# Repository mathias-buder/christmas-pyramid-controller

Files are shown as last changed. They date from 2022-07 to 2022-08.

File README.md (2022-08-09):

- [Introduction](#introduction)
- [The Christmas Pyramid](#the-christmas-pyramid)
- [Control Unit Design](#control-unit-design)
  - [Requirement Definition](#requirement-definition)
  - [System Architecture](#system-architecture)
    - [CPU Board](#cpu-board)
  - [Sound Card](#sound-card)
  - [UART-RF Bridge](#uart-rf-bridge)
  - [Electronical Design](#electronical-design)
  - [Final Device Layout](#final-device-layout)
  - [Software Architecture](#software-architecture)
    - [Software Layer Stackup](#software-layer-stackup)
    - [Source Code Layout](#source-code-layout)
    - [Persistent Memory Scheme](#persistent-memory-scheme)
    - [Main Control Loop Flow](#main-control-loop-flow)
  - [Command Line Interface](#command-line-interface)
    - [Command Structure](#command-structure)
    - [Output Format](#output-format)
      - [Real-Time Clock / Temperature](#real-time-clock--temperature)
      - [Task List](#task-list)
    - [Command List](#command-list)

# Introduction
Some time ago, my dad called me to tell me that he is planing to build a giant christmas pyramid that is supposed to be placed in front of the local church at christmas time. The setting up should take place in the form of a Christmas party where everyone comes together and drinks mulled wine.

**What a great idea I thought!**

As the pyramid was to remain standing for the entire Christmas season, a control unit was needed for automatic operation.

# The Christmas Pyramid
As can be seen below, the pyramid contains a number of lamps (230 VAC) as well as a motor (230 VAC) for turning the wings.

<p align="center">

</p>

# Control Unit Design
This section is going to describe the control unit design process.

## Requirement Definition
The ECU shall satisfy the following list of requirements:
- Shall have the ability to switch multiple 230 VAC actors (at least 2 individually)
- Shall have to ability to detect motion from humans that move in front of the pyramid
- Shall be able to play music
  - that is stored on an SD Card / USB thumb drive
  - that is in .mp3 and .wav format
  - that is automatically played based on motion sensor input
  - that is outputted through a standard 3.5mm audio jack to be fed to an audio amplifier
- shall have an interface to re-programmed the firmware image
- shall have the ability to be accessed over the air
- shall have the ability to setup tasks in which the user can specify
  - task activation/deactivation time
  - is music playback active/inactive
  - duration of music playback
  - is motion detection active/inactive
  - which AC-actor switch shall be active/inactive
- Shall operate within the temperature range of -20°C - 40°C

## System Architecture
The overall system architecture is shown in the block diagram below. The basic idea is to use as many off-the-shelf components as possible and interconnect them using a custom designed carrier board.

1. 80 MHz ARM Cortex-M4 µC TM4C123GH6PMI
2. Two-line dot-matrix display NHD-0216K3Z-NSW-BBW-V3
3. Endless rotary push encoder
4. UART-RF radio module HM-TRP
5. SD card interface 
6. USB 2.0 interface 
7. Sound card with VSI 003 audio codec
8. Real-time clock (incl. temperature sensor) DS3231
9. EEPROM 32KByte
10. 8-channel relay board (230VAC IOA)
11. Infrared motion sensor HCSR501

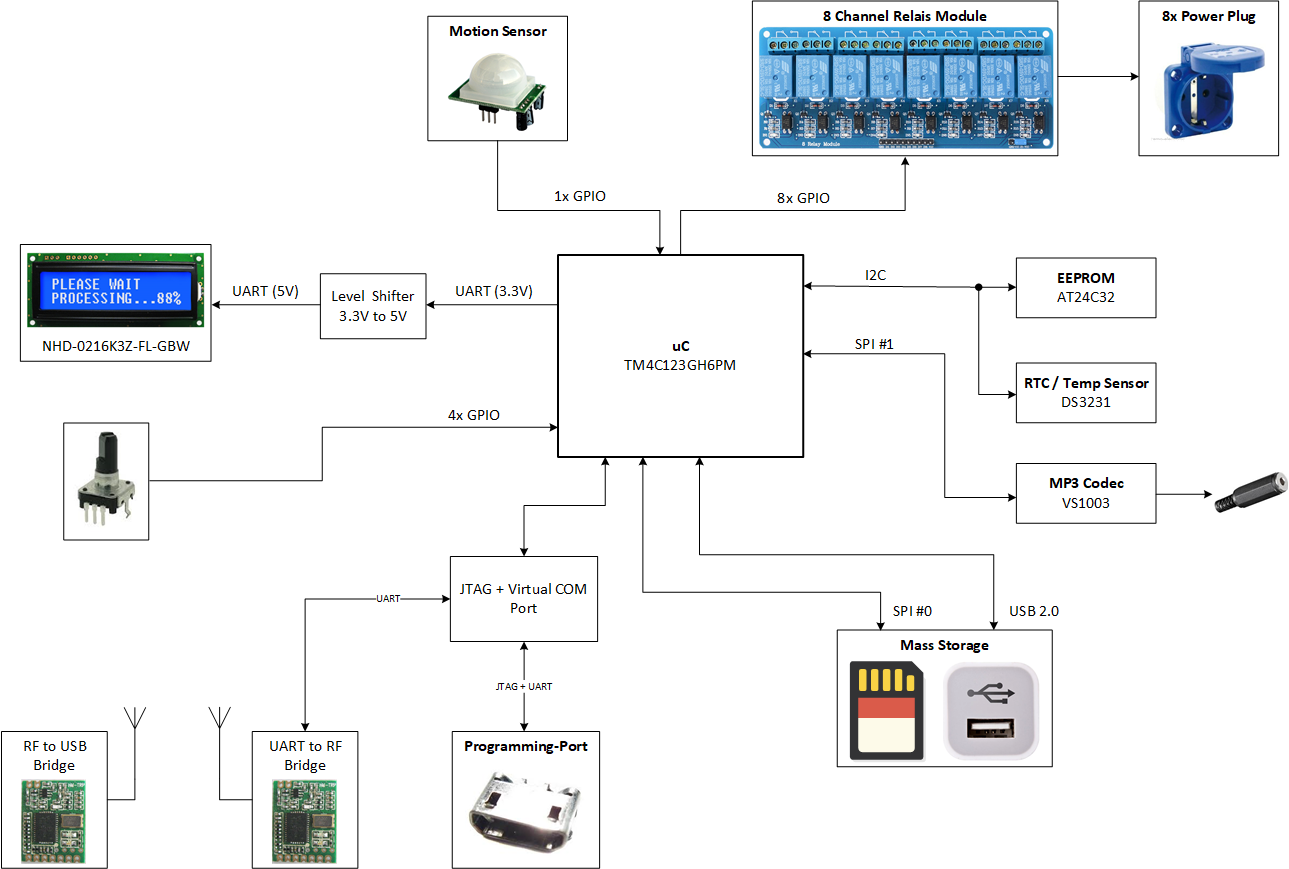
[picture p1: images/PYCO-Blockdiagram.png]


### CPU Board
As central processing unit the evaluation kit [EK-TM4C123GXL](https://www.ti.com/tool/EK-TM4C123GXL) from TI has been used. This board offers:

* 80 MHz ARM Cortex-M4 (TM4C123GH6PMI)
* On-Board ICD (JTAG) incl. an virtual serial port over a single USB connection
* USB 2.0 interface for e.g. mass-storage interface
* On-Board clocking incl. LFO for real-time clock applications
* Rich expansion header to interface with all available peripherals
* Rich, free and easy-to-use API provided by TI
* __Cost on 10 EUR__

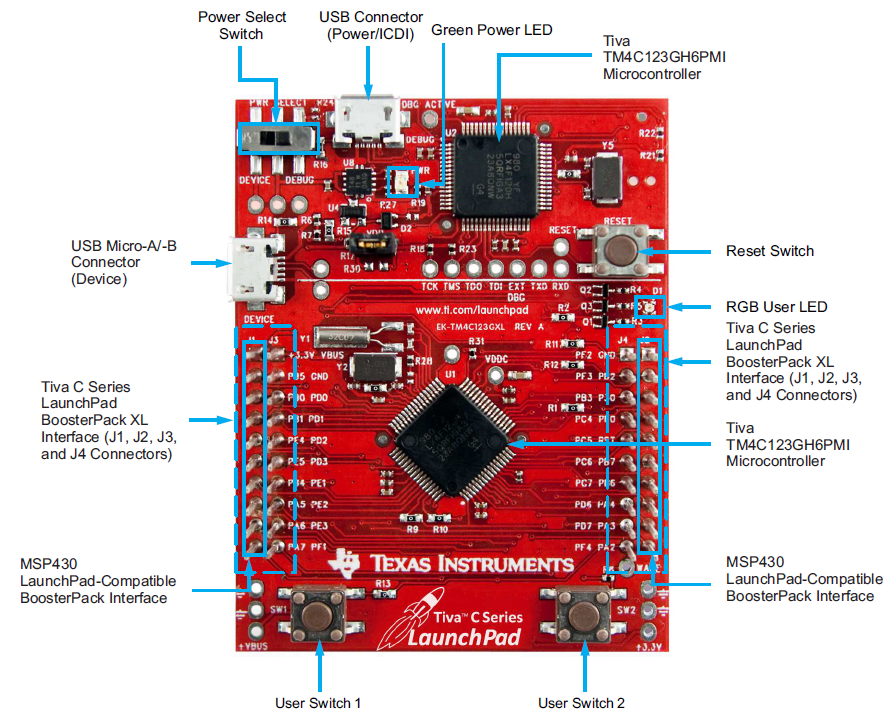
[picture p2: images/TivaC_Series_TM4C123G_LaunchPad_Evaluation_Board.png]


## Sound Card
To enable the device to play audio in .mp3 and .wav format the audio codec [VS1003 from VLSI solution](electronical%20design/components/02_Audio_Codec/VS1003.pdf) has been utilized. It connects to an MCU over an SPI interface and accepts a raw data stream of many codecs like MP3, WMA, RIFF WAV amd MIDI formats. In addition, it provides the capability to adjust the output volume by software which enables flexible audio fade-in/out.

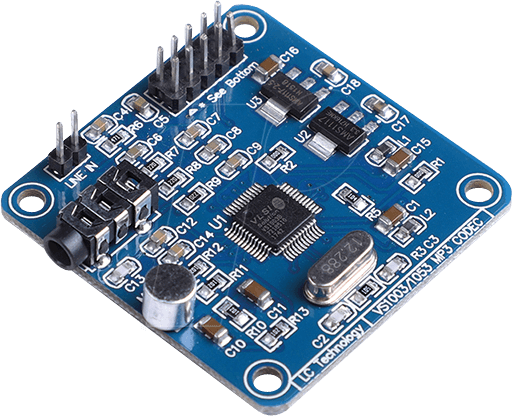
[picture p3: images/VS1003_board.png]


## UART-RF Bridge
The system will be equipped with an software bootload that allows to update the software of the virtual serial port. As this update is required to be performed over the air the UART-to-RF bridge [HM-TRP](electronical%20design/components/09_RF/HM-TRP.pdf) has been utilized.

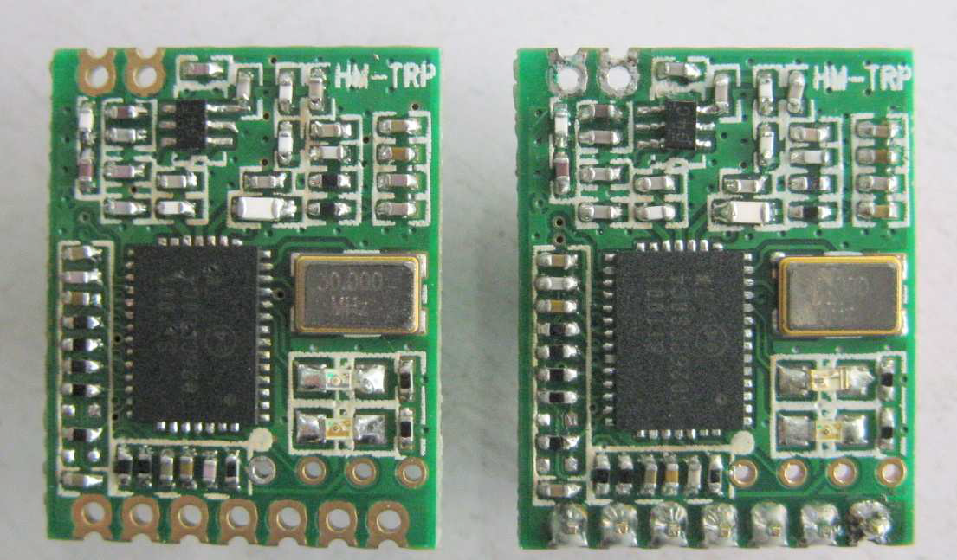
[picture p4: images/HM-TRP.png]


Two custom boards have been designed to allow the [HM-TRP](electronical%20design/components/09_RF/HM-TRP.pdf) to interface with thw MCUs virtual serial port and the remote computer.

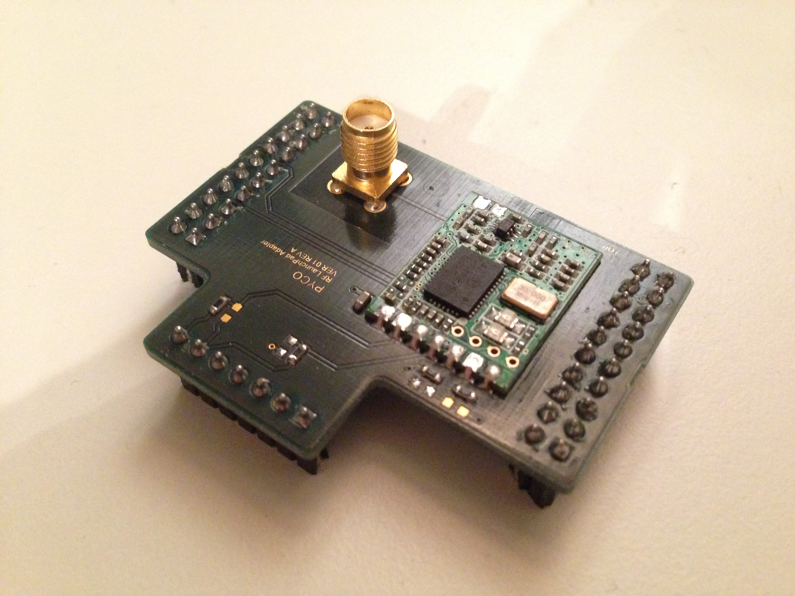
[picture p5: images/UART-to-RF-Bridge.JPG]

<center>MCU side RF adapter</center>
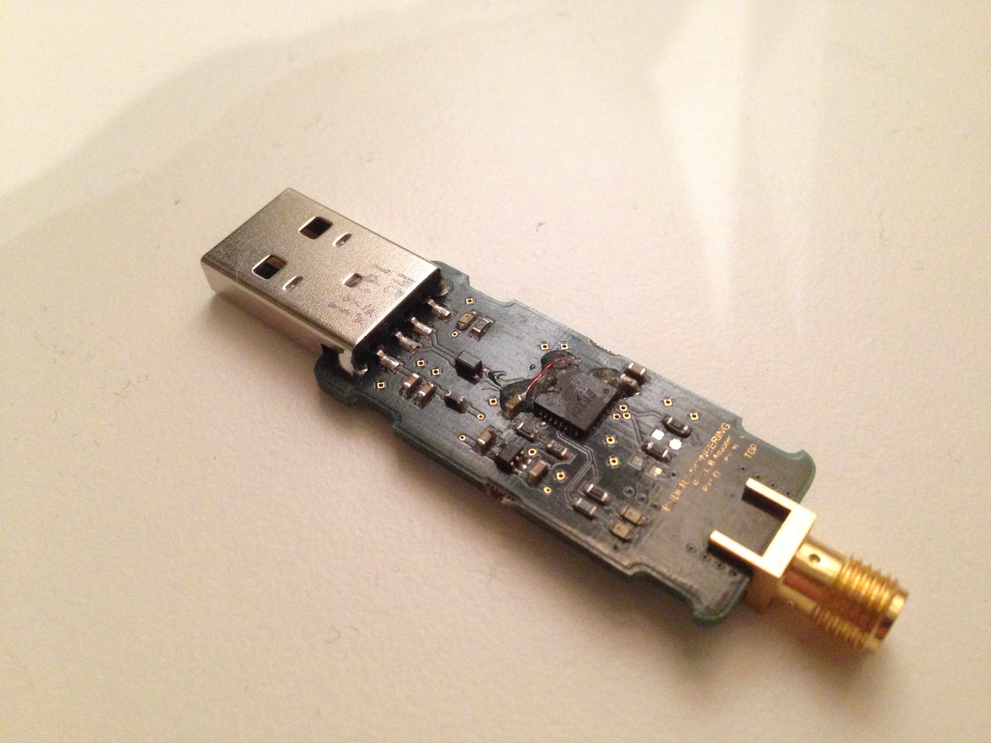
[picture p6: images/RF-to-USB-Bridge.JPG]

<center>Remote PC side RF adapter</center>

## Electronical Design
All schematics can be found within the [electronical design](electronical%20design/schematics/) folder.

* [Main Board](electronical%20design/schematics/main%20board/PYRAMIDE%20CONTROLLER.pdf)
* [UART to RF Bridge](electronical%20design/schematics/UART%20to%20RF%20Bridge/RfLauchPadAdapter.pdf)
* [USB to RF Bridge](electronical%20design/schematics/USB%20%20to%20RF%20Bridge/RfUsbAdapter.pdf)

The final result after the PCB schematics capture and layout phase can be seen below.

__Note: The RF-to-UART board isn't attached on these images. It would be stacked on top of the EK-TM4C123GXL evaluation kit.__

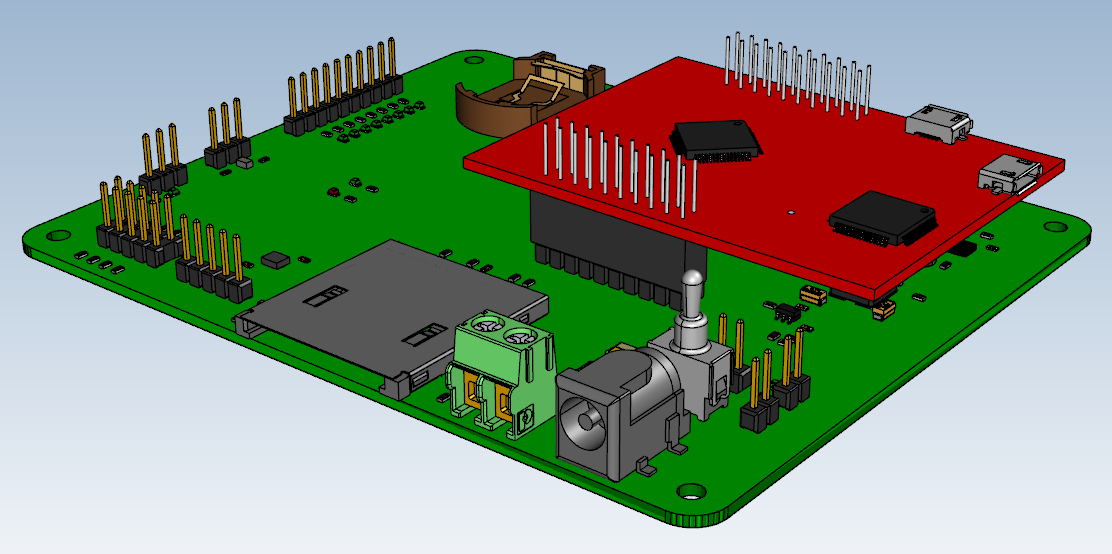
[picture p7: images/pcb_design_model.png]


## Final Device Layout
The final result of the assembled device incl. its enclosure can be seen below.
<p align="center">
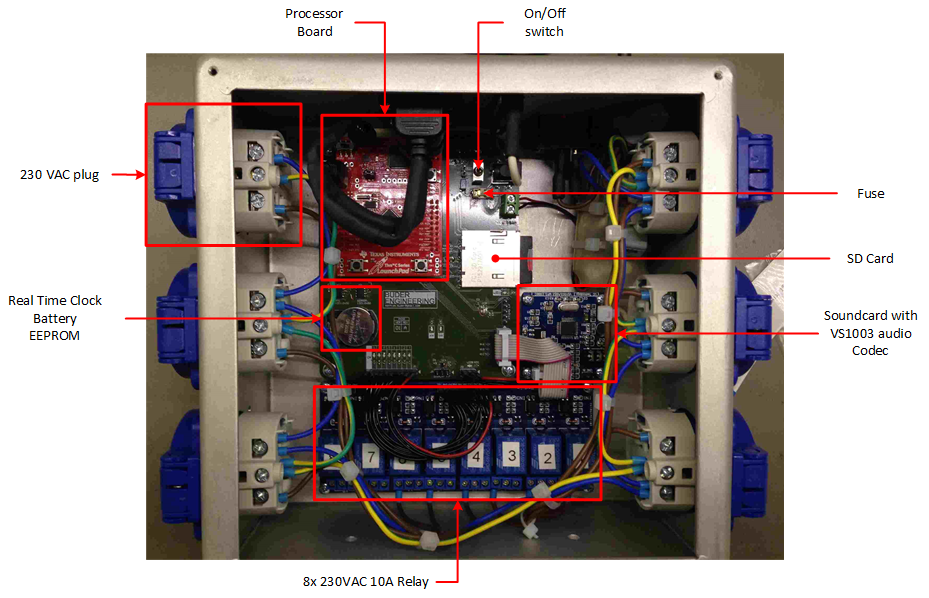
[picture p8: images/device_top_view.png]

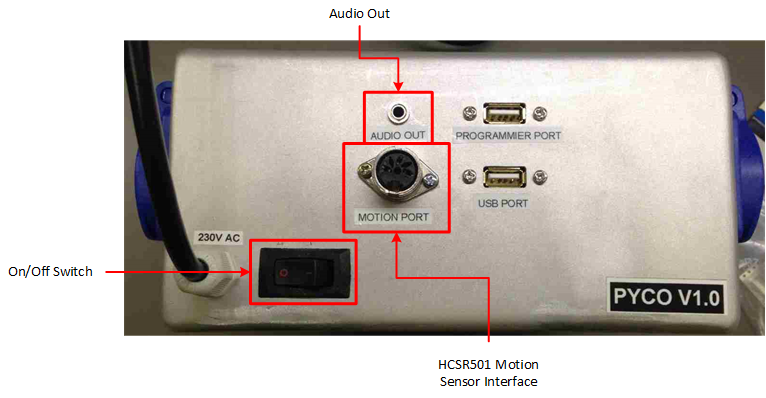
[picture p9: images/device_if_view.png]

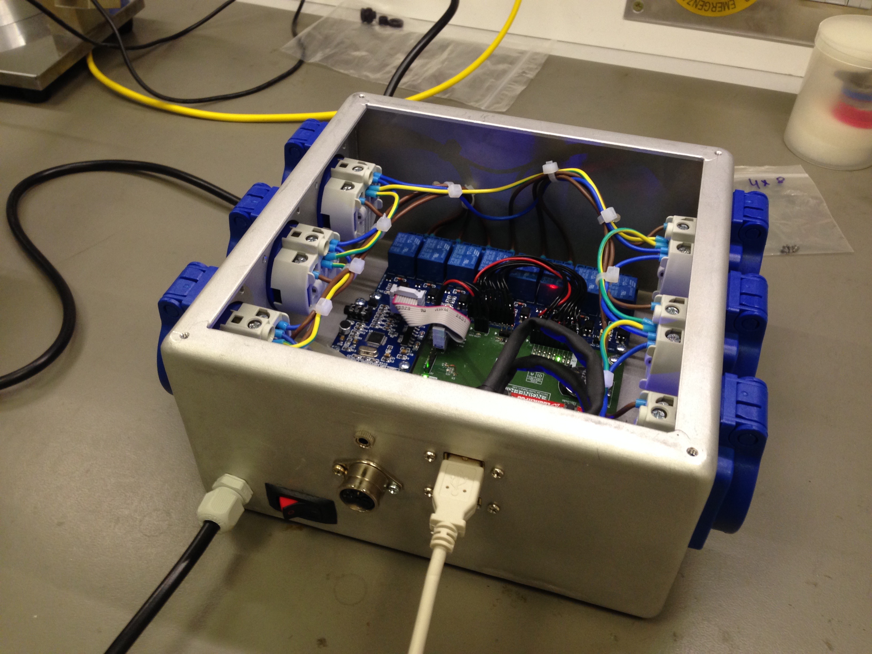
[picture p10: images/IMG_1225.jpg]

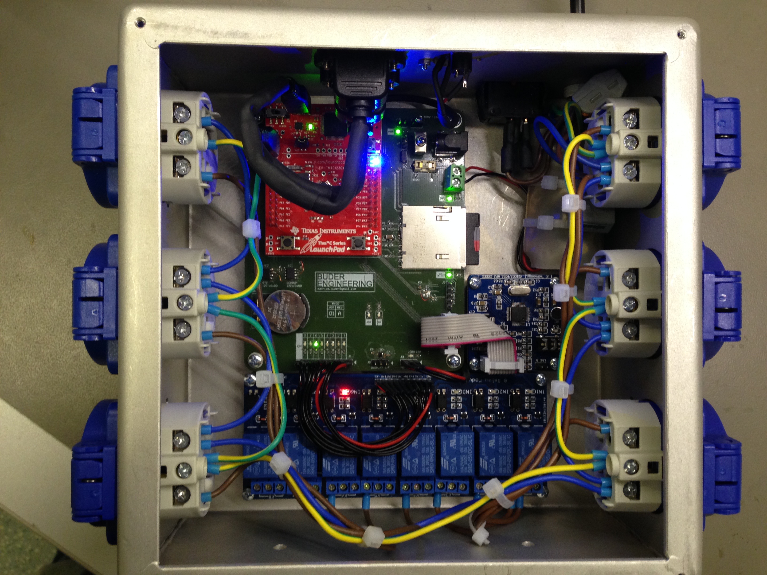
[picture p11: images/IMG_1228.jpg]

</p>

## Software Architecture

### Software Layer Stackup
The software has been broken into individual software components that where stacked onto each other and exchange data over a defined software interface.

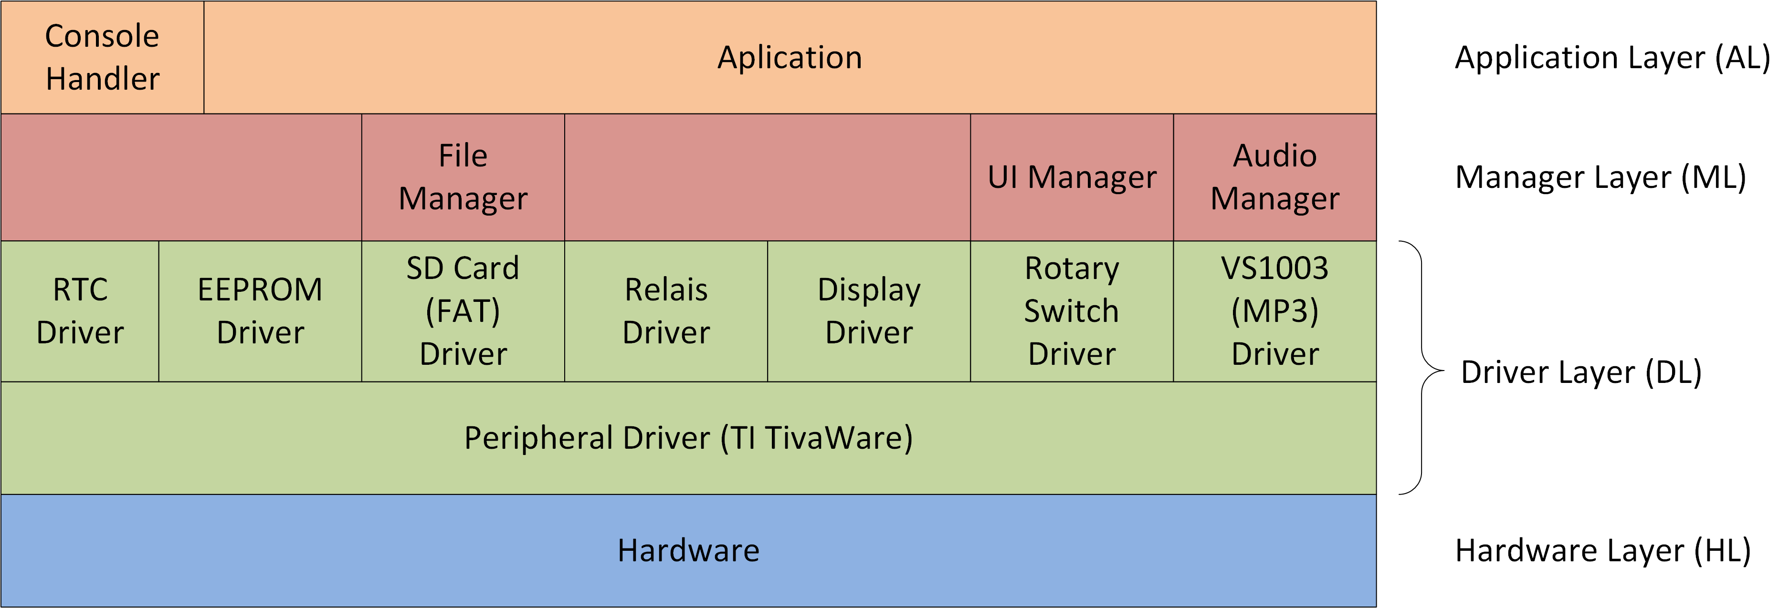
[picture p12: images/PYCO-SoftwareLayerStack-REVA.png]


### Source Code Layout
- [Application](/software/main.c)
  - Global Initialization based on [System.c](/software/System.c)
  - [Main Control Loop](/images/MainControlLoop.png)
- [System Configuration](/software/System.c)
- [Manager](/software/Manager)
  - [Audio Manager](/software/Manager/AudioManager.c)
  - [Console Manager](/software/Manager/ConsoleManager.c)
  - [Display Manager](/software/Manager/DisplayManager.c)
  - [File Manager](/software/Manager/FileManager.c)
  - [Task Manager](/software/Manager/TaskManager.c)
- Utilities
  - [Command Line Handler](/software/utils/cmdline.c)
  - [UART stdio Interface Driver](/software/utils/uartstdio.c)
- Handy Macros
  - [stdio command line macros](/software/Msg.h)

### Persistent Memory Scheme
All data that is required to be saved persistently is stored onto the SD card into the following two files:

* system.cfg
  
  Data is saved into an binary blob having the following format (specified in [System.h](software/System.h)):
  ```C
  typedef struct {
    uint8_t ui8Mode;                  // Switch between 0: Manuel, 1: Auto mode
    uint8_t ui8DefaultVolume;         // Default volume
    uint8_t ui8DefaultFadeTime;       // Default fade-in/out time (s)
    bool    bAutoSave;                // Enable/Disable auto-save-mode
    uint8_t ui8DefaultDsplContrast;   // Default display contrast
    uint8_t ui8DefaultDsplBrightness; // Default display brightness
    TIME    sDefaultActiveTime;       // Default active time
    uint8_t ui8DefaultMotionDelay;    // Default motion delay (s)
  }SYSTEM;
  ```

* task.cfg

  Data is saved into an binary blob having the following format [TaskManager.h](software/Manager/TaskManager.h)):
  ```C
  typedef struct {
    int16_t i16Id;                 // task id
    TIME    sStartTime;            // start time (hh:mm:ss)
    TIME    sStopTime;             // stop time (hh:mm:ss)
    TIME    sActiveTime;           // motion event aktive time (hh:mm:ss)
    bool    bMotion;               // motion active flag
    bool    bAudio;                // audio active flag
    bool    bActuator;             // actuator active flag
    bool    bActuatorCH[ACT_N_CH]; // active actuator channel no.
    uint8_t ui8ActuatorProg;       // actuator program (runns when actuators are activated)
  }TASK;
  ```

### Main Control Loop Flow
The software has been design in a way that all runs within a single runnable instance. To accomplish the parallel processing of the main control loop, the Audio and UART handling an interrupt mechanism is used.

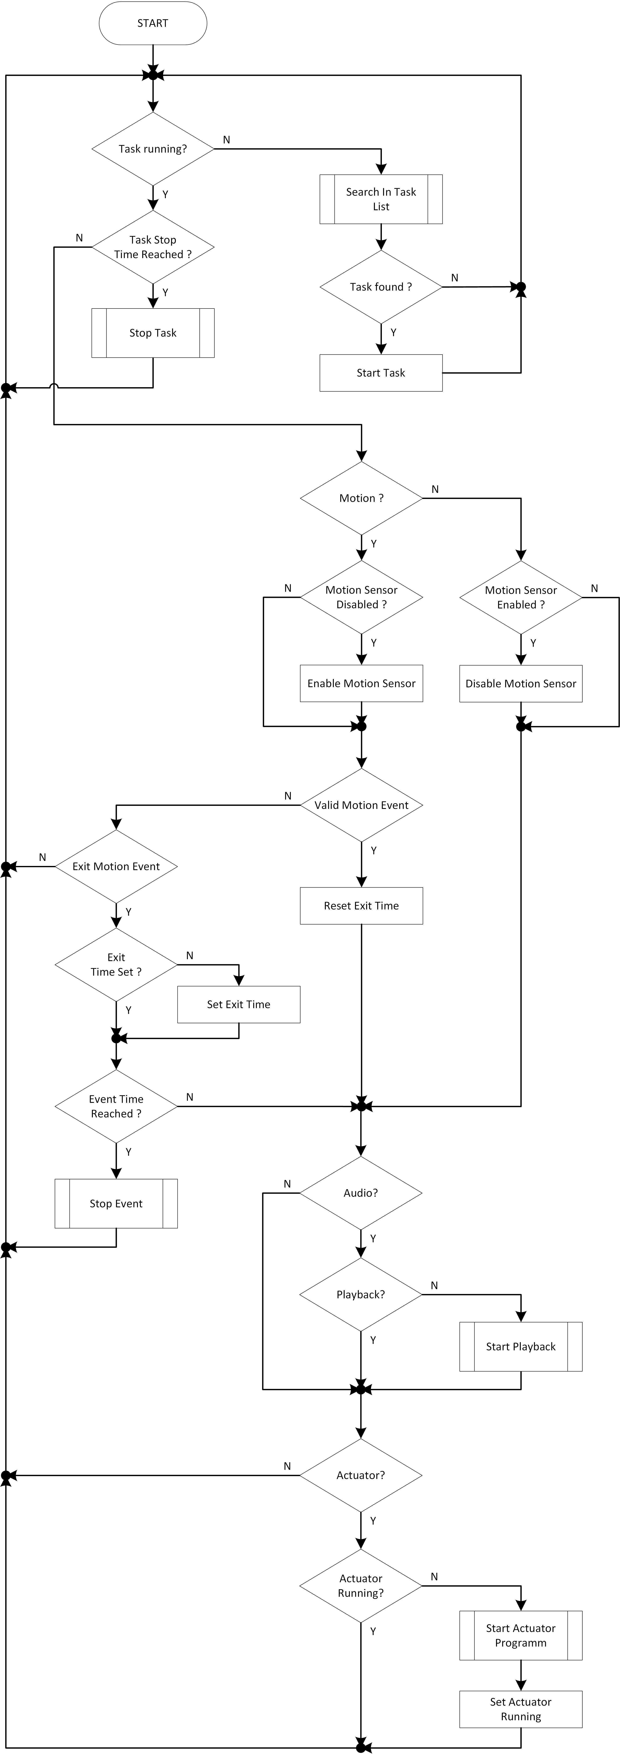
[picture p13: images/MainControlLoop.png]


## Command Line Interface

The system configuration is done over UART using the RF-to-USB adapter. This, when used on a Windows system, emulates a serial interface (COM port) and can be used in conjunction with a console programme (Putty, hTerm, ...) to configure the system at hand. The following parameters shall be set for communication:

| | |
| --- | --- |
| Baudrate | 9600 |
| Databits | 8 |
| Stopbit | 1 |
| Parity | none |
| CTS| none |

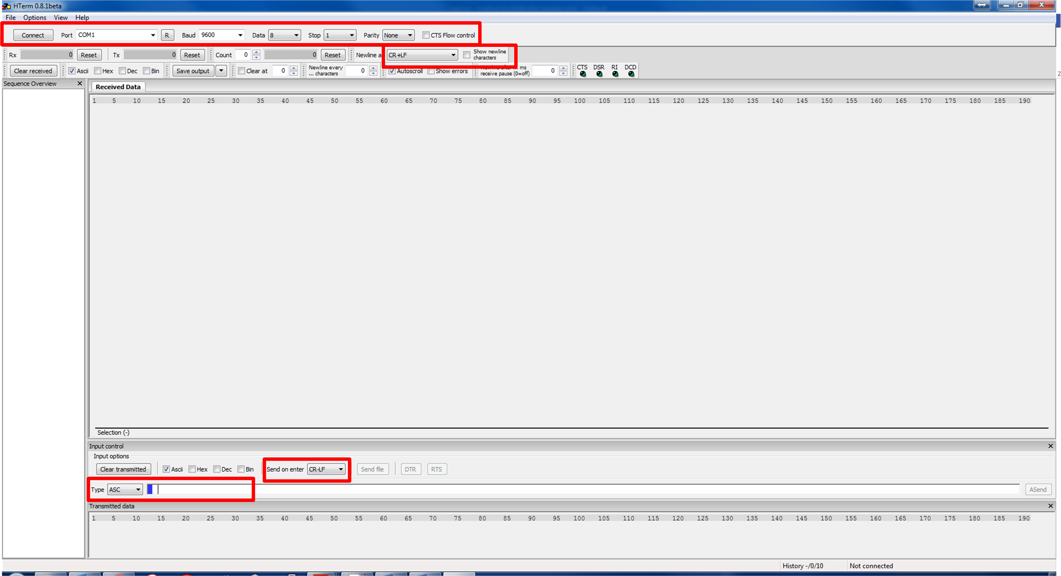
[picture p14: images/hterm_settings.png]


### Command Structure
The command parser uses the standard command-paramater-value structure as shown below:

`<COMMAND> -<PARAM_1> <VALUE_1> -<PARAM_2> <VALUE_2> ... -<PARAM_N> <VALUE_N>`

*Example: Set RTC to date 15.02.1983*

`z -dd 15 -mm 02 -yy 1982`

Parameters can also be used individually. The command above contains a typo as the year is set to 1982. Lets correct it by issuing command:

`z -yy 1983`

### Output Format

#### Real-Time Clock / Temperature
The output format of the RTC and temperature component can be seen below.

Date Format : `<Day of week> <Day> <Month> <Year>`\
Time Format : `<Hour> <Minute> <Second>`\
Temperature Format : `<##.##>` °C
 


#### Task List
The output format of the task list can be seen below. Each task can be individually configured using the commands listed in section [Command List](#command-list) below.


### Command List

| Description | Command | Parameter | Value Range |
| --- | :---: | --- | --- |
| __General__ |
| Show all available commands | ? | - | - |
| Clear console history | cls | - | - |
| Save task list to file <br> (see [task.cfg](#persistent-memory-scheme) for details) | spa | - | - |
| Save system parameter to file <br> (see [system.cfg](#persistent-memory-scheme) for details) | sps | - | - |
| Load task list and system configuration from file <br> (see [task.cfg, system.cfg](#persistent-memory-scheme) for details) | lad | - | - |
| __Task Management__ |
| Display task list | aa | - | - |
| Add new task | ah | - | - |
| Remove task | ae | `<TASK_ID>` | 1 - 25 |
| Update task | ab | -a `<TASK_ID>` <br> -sah `<START_HOUR>` <br> -sam `<START_MINUTE>` <br> -sah `<STOP_HOUR>` <br> -sam `<STOP_MINUTE>`  <br> -akm `<ACTIVE_MINUTE>` <br> -aks `<ACTIVE_SECOND>` <br> -b `<MOTION_SENSOR_FLAG>` <br> -au `<AUDIO_PLAYBACK_FLAG>` <br> -akt `<ACTUATOR_FLAG>` <br> -ak `<ACTUATOR_CHANNEL>`| 1 - 25 <br> 0 - 23 [h] <br> 0 - 59 [m] <br> 0 - 23 [h] <br> 0 - 59 [m] <br> 0 - 59 [m] <br> 0 - 59 [m] <br> 0: Off, 1: On <br> 0: Off, 1: On <br> 0: Off, 1: On <br> 1 - 8|
| __System Parameter__ |
| Display system parameter | sa | - | - |
| Set operation mode <br> Set default playback volume <br> Set default audio playback fade-in time <br> Set default display contrast <br> Set default display brightness <br> Set default audio playback active time [m] <br> Set default audio playback active time [s] <br> Set motion detection debounce time | sb | -m `<MODE>` <br> -v `<DEFAULT_VOLUME>` <br> -ebz `<DEFAULT_FADE_IN_OUT_TIME>` <br> -dc `<DEFAULT_DISPLAY_CONTRAST>` <br> -db `<DEFAULT_DISPLAY_BRIGHTNESS>`  <br> -atm `<DEFAULT_ACTIVE_MINUTE>` <br> -ats `<DEFAULT_ACTIVE_SECOND>` <br> -bvz `<MOTION_DETECTION_DELAY>` | 0: Auto, 1: Manuel <br> 0 - 100 [%] <br> 0 - 60 [s] <br> 1 - 50 <br> 1 - 8 <br> 0 - 59 [s] <br> 0 - 59 [s] <br> 0 - 59 [s]
| __Audio Management__ |
| Playback audio | play | `<PATH_TO_AUDIO_FILE>` | - |
| Pause audio | pause | - | - |
| Stop audio | stop | - | - |
| Adjust audio volume | lst | `<VOLUME>` | 0 - 100 [%] |
| Adjust audio fade-in time | einbl | `<TIME>` | 0 - 60 [s] |
| Adjust audio fade-out time | ausbl | `<TIME>` | 0 - 60 [s] |
| __SD Card Management__ |
| List content | ls | - | - |
| Change directory | cd | `<DIR_NAME>` | - |
| Move one directory level up | cd .. | - | - |
| Print working directory | pwd | - | - |
| Print file content | cat | `<FILE_NAME>` | - |
| Remove file/folder | rm | `<FILE/FOLDER_NAME>` | - |
| Index audio files<br>(Is done at every start-up) | index | - | - |
| __Real-Time Clock (RTC) Management__ |
| Show all available commands <br> Show Time, Date amd Temperature <br> Set day of week <br> Set day <br> Set Month <br> Set Year <br> Set Hour <br> Set Minute <br> Set Second| z | -? <br> -a <br> -wt `<DAY_OF_WEEK>` <br> -dd `<DAY>` <br> -mm `<MONTH>` <br> -yy `<YEAR>` <br> -h `<HOUR>` <br> -m `<MINUTE>` <br> -s `<SECOND>` | - <br> - <br> Mo, Di, Mi, Do, Fr, Sa, So <br> 1 - 31 <br> 1 - 12 <br> 0 - 99 <br> 0 - 23 <br> 0 - 59 <br> 0 - 59
| __Display Management__ |
| Adjust contrast <br> Adjust brightness | disp | -c `<CONTRAST>` <br> -b `<BRIGHTNESS>` | 1 - 50 <br> 1 - 8|
| __Actuator Management__ |
| Enable relay <br> Disable relay <br> Enable all relays <br> Disable all relays | rly | -an `<CHANNEL_NO>` <br> -aus `<CHANNEL_NO>` <br> -allean <br> -alleaus| 1 - 8 <br> 1 - 8 <br> - <br> -|

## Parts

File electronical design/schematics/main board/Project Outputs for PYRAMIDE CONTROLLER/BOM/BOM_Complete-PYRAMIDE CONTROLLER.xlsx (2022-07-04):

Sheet: Part List Report
Component list
 | TITLE | Pyramide Controller |  | REPORT DATE | 2015-11-18 | 22:36:21
 | PROJECT | PYCO |  | PRINT DATE | 2022-07-04 | 9:38:08
 | COMPONENT | BABO
 | VERSION | 01
 | REVISION | A
 | SOURCE FILE | PYRAMIDE CONTROLLER VER01 REVA.PrjPcb
 | VARIANT | None
# | Category | Manufacturer 1 | Manufacturer Part Number 1 | Package / Case | Description | Quantity | Supplier 1 | Supplier Part Number 1 | Supplier Order Qty 1 | Supplier Stock 1 | Supplier Unit Price 1 | Supplier Subtotal 1 | Supplier Currency 1
1 | Programmers, Development Systems | Texas Instruments | EK-TM4C123GXL |  | EVAL KIT TM4C123GXL LAUNCHPAD | 1 | Digi-Key | 296-35760-ND | 2 | 2823 | 12.22 | 24.44 | EUR
2 | Integrated Circuits (ICs) | Maxim Integrated | DS3231MZ/V+ | 8-SOIC (0.154", 3.90mm Width) | IC RTC CLK/CALENDAR I2C 8-SOIC | 1 | Digi-Key | DS3231MZ/V+-ND | 2 | 1414 | 5.97 | 11.94 | EUR
3 | Circuit Protection | Littelfuse Inc. | 0154.062DR | 2-SMD, Square End Block with Holder | FUSE BRD MNT 62MA 125VAC/VDC SMD | 1 | Digi-Key | F3148CT-ND | 2 | 2330 | 4.17 | 8.34 | EUR
4 | Connectors, Interconnects | FCI | 10067847-001RLF |  | CONN SD CARD PUSH-PUSH SMD | 1 | Digi-Key | 609-3956-1-ND | 2 | 9437 | 2.56 | 5.12 | EUR
5 | Switches | Copal Electronics Inc. | ATE1E-2M3-10-Z |  | SWITCH TOGGLE SPDT 50MA 48V | 1 | Digi-Key | 563-1159-ND | 2 | 2717 | 2.6 | 5.2 | EUR
6 | Integrated Circuits (ICs) | Texas Instruments | TPS62152RGTT | 16-VFQFN Exposed Pad | IC REG BUCK 3.3V 1A SYNC 16QFN | 1 | Digi-Key | 296-30009-1-ND | 2 | 2622 | 2.4 | 4.8 | EUR
7 | Connectors, Interconnects | CUI Inc. | PJ-002AH-SMT-TR |  | CONN POWER JACK 2.1X5.5MM HI CUR | 1 | Digi-Key | CP-002AHPJCT-ND | 2 | 79972 | 1.71 | 3.42 | EUR
8 | Integrated Circuits (ICs) | Texas Instruments | TPS563200DDCT | SOT-23-6 Thin, TSOT-23-6 | IC REG BUCK ADJ 3A SYNC 6SOT | 1 | Digi-Key | 296-38434-6-ND | 2 | 3243 | 1.39 | 2.78 | EUR
9 | Integrated Circuits (ICs) | Microchip Technology | 24AA512-I/SN | 8-SOIC (0.154", 3.90mm Width) | IC EEPROM 512KBIT 400KHZ 8SOIC | 1 | Digi-Key | 24AA512-I/SN-ND | 2 | 6462 | 1.16 | 2.32 | EUR
10 | Optoelectronics | Lite-On Inc. | LTST-C193KGKT-5A | 0603 (1608 Metric) | LED GREEN CLEAR 0603 SMD | 15 | Digi-Key | 160-1828-6-ND | 30 | 75885 | 0.268 | 8.04 | EUR
11 | Battery Products | Harwin Inc. | S8421-45R |  | HOLDER BATT COIN CR2032/20MM | 1 | Digi-Key | 952-1737-1-ND | 2 | 9511 | 0.97 | 1.94 | EUR
12 | Capacitors | TDK Corporation | C3216X6S1A476M160AC | 1206 (3216 Metric) | CAP CER 47UF 10V X6S 1206 | 1 | Digi-Key | 445-6010-6-ND | 2 | 20133 | 0.96 | 1.92 | EUR
13 | Integrated Circuits (ICs) | NXP Semiconductors | NTB0104BQ,115 | 14-VFQFN Exposed Pad | TXRX TRANSLATING 3STATE 14DHVQFN | 1 | Digi-Key | 568-8404-1-ND | 2 | 11153 | 0.83 | 1.66 | EUR
14 | Inductors, Coils, Chokes | Bourns Inc. | SRR6038-3R3Y | Nonstandard | FIXED IND 3.3UH 3.5A 20 MOHM SMD | 1 | Digi-Key | SRR6038-3R3YCT-ND | 2 | 865 | 0.62 | 1.24 | EUR
15 | Discrete Semiconductor Products | Micro Commercial Co | SK36A-LTP | DO-214AC, SMA | DIODE SCHOTTKY 60V 3A DO214AC | 1 | Digi-Key | SK36A-LTPMSDKR-ND | 2 | 43945 | 0.52 | 1.04 | EUR
16 | Inductors, Coils, Chokes | Bourns Inc. | SDR0403-2R2ML | Nonstandard | FIXED IND 2.2UH 2.6A 47 MOHM SMD | 1 | Digi-Key | SDR0403-2R2MLCT-ND | 2 | 9256 | 0.43 | 0.86 | EUR
17 | Integrated Circuits (ICs) | NXP Semiconductors | 74LVC1T45GW,125 | 6-TSSOP, SC-88, SOT-363 | TXRX XLATING DUAL 3ST 6TSSOP | 1 | Digi-Key | 568-5461-1-ND | 2 | 57825 | 0.41 | 0.82 | EUR
18 | Kondensatoren | Kemet | T491A106K016AT |  | CAP TANT 10UF 16V 10% 1206 | 2 | Digi-Key | 399-8269-1-ND | 4 | 97831 | 0.38 | 1.52 | EUR
19 | Connectors, Interconnects | Phoenix Contact | 1935161 |  | TERM BLOCK PCB 2POS 5.0MM GREEN | 1 | Digi-Key | 277-1667-ND | 2 | 20836 | 0.34 | 0.68 | EUR
20 | Optoelectronics | Lite-On Inc. | LTST-C193KRKT-5A | 0603 (1608 Metric) | LED RED CLEAR 0603 SMD | 1 | Digi-Key | 160-1830-1-ND | 2 | 115279 | 0.34 | 0.68 | EUR
21 | Capacitors | TDK Corporation | C2012X5R0J226M125AC | 0805 (2012 Metric) | CAP CER 22UF 6.3V X5R 0805 | 1 | Digi-Key | 445-1422-6-ND | 2 | 411958 | 0.26 | 0.52 | EUR
22 | Capacitors | Murata Electronics North America | GRM1885C1H391JA01D | 0603 (1608 Metric) | CAP CER 390PF 50V NP0 0603 | 1 | Digi-Key | 490-1441-1-ND | 2 | 38397 | 0.14 | 0.28 | EUR
23 | Resistors | Panasonic Electronic Components | ERJ-3EKF1002V | 0603 (1608 Metric) | RES SMD 10K OHM 1% 1/10W 0603 | 1 | Digi-Key | P10.0KHCT-ND | 2 | 4723247 | 0.09 | 0.18 | EUR
24 | Resistors | Panasonic Electronic Components | ERJ-3EKF1003V | 0603 (1608 Metric) | RES SMD 100K OHM 1% 1/10W 0603 | 12 | Digi-Key | P100KHCT-ND | 24 | 3322184 | 0.09 | 2.16 | EUR
25 | Resistors | Panasonic Electronic Components | ERJ-3EKF2000V | 0603 (1608 Metric) | RES SMD 200 OHM 1% 1/10W 0603 | 1 | Digi-Key | P200HCT-ND | 2 | 1198868 | 0.09 | 0.18 | EUR
26 | Resistors | Panasonic Electronic Components | ERJ-3EKF2201V | 0603 (1608 Metric) | RES SMD 2.2K OHM 1% 1/10W 0603 | 2 | Digi-Key | P2.20KHCT-ND | 4 | 988101 | 0.09 | 0.36 | EUR
27 | Resistors | Panasonic Electronic Components | ERJ-3EKF2401V | 0603 (1608 Metric) | RES SMD 2.4K OHM 1% 1/10W 0603 | 2 | Digi-Key | P2.40KHCT-ND | 4 | 98821 | 0.09 | 0.36 | EUR
28 | Resistors | Panasonic Electronic Components | ERJ-3EKF3300V | 0603 (1608 Metric) | RES SMD 330 OHM 1% 1/10W 0603 | 13 | Digi-Key | P330HCT-ND | 26 | 505878 | 0.09 | 2.34 | EUR
29 | Resistors | Panasonic Electronic Components | ERJ-3EKF5602V | 0603 (1608 Metric) | RES SMD 56K OHM 1% 1/10W 0603 | 1 | Digi-Key | P56.0KHCT-ND | 2 | 272979 | 0.09 | 0.18 | EUR
30 | Resistors | Panasonic Electronic Components | ERJ-3EKF7500V | 0603 (1608 Metric) | RES SMD 750 OHM 1% 1/10W 0603 | 1 | Digi-Key | P750HCT-ND | 2 | 368970 | 0.09 | 0.18 | EUR
31 | Resistors | Panasonic Electronic Components | ERJ-3GEY0R00V | 0603 (1608 Metric) | RES SMD 0 OHM JUMPER 1/10W | 4 | Digi-Key | P0.0GCT-ND | 8 | 7280017 | 0.09 | 0.72 | EUR
32 | Kondensatoren | Kemet | C0603C104J4RACTU |  | CAP CER 100NF 16V 5% X7R 0603 | 9 | Digi-Key | 399-1097-1-ND | 18 | 868511 | 0.07 | 1.26 | EUR
 |  |  |  |  |  | 83 |  |  | 166 |  |  | 97.48
 |  |  |  |  |  | 2 | pcs: | Total |  | 97.48 |  | EUR
 |  |  |  |  |  |  |  | Price for 1pcs |  | 48.74 |  | EUR

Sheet: Project Information
Project Full Path | C:\Users\Nano\Google Drive\Projekte\PYRAMIDE_CONTROLLER\02_Electronical_Design\02_Schematic\VER01\REVA\PYRAMIDE CONTROLLER VER01 REVA.PrjPcb
Project Filename | PYRAMIDE CONTROLLER VER01 REVA.PrjPcb
Variant Name | None
Data-Source Filename | PYRAMIDE CONTROLLER VER01 REVA.PrjPcb
Data-Source Full Path | C:\Users\Nano\Google Drive\Projekte\PYRAMIDE_CONTROLLER\02_Electronical_Design\02_Schematic\VER01\REVA\PYRAMIDE CONTROLLER VER01 REVA.PrjPcb
Title | Bill of Materials For Project [PYRAMIDE CONTROLLER VER01 REVA.PrjPcb] (No PCB Document Selected)
Total Quantity | 96
Report Time | 22:36:21
Report Date | 18.11.2015
Report Date & Tine | 18.11.2015 22:36:21
Output Name | Bill of Materials
Output Type | BOM_PartType
Output Generator Name | BOM
Output Generator Description | Bill of Materials

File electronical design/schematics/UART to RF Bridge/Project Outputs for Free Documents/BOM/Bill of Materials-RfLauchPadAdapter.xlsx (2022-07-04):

Category | Manufacturer 1 | Manufacturer Part Number 1 | Package / Case | Description | Quantity | Supplier 1 | Supplier Part Number 1 | Supplier Order Qty 1 | Supplier Stock 1 | Supplier Subtotal 1 | Supplier Unit Price 1 | Supplier Currency 1
Connectors, Interconnects | TE Connectivity AMP Connectors (https://octopart-clicks.com/click/altium?manufacturer=TE%20Connectivity%20AMP%20Connectors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) | 5-1814832-1 (https://octopart-clicks.com/click/altium?manufacturer=TE%20Connectivity%20AMP%20Connectors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) |  | CONN SMA JACK STR 50 OHM PCB | 1 | Digi-Key | A97594-ND (https://octopart-clicks.com/click/altium?manufacturer=TE%20Connectivity%20AMP%20Connectors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) | 2 | 19120 | 3,5 | 1,75 | EUR
Capacitors | Murata Electronics North America (https://octopart-clicks.com/click/altium?sku=490-1536-1-ND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) | GRM188R61C105KA93D (https://octopart-clicks.com/click/altium?sku=490-1536-1-ND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) | 0603 (1608 Metric) | CAP CER 1UF 16V 10% X5R 0603 | 1 | Digi-Key | 490-1536-1-ND (https://octopart-clicks.com/click/altium?sku=490-1536-1-ND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) | 2 | 721477 | 0,28 | 0,14 | EUR
Resistors | Panasonic Electronic Components (https://octopart-clicks.com/click/altium?manufacturer=Panasonic%20Electronic%20Components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) | ERJ-3EKF1002V (https://octopart-clicks.com/click/altium?manufacturer=Panasonic%20Electronic%20Components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) | 0603 (1608 Metric) | 10K OHM 1% 1/10W 0603 | 4 | Digi-Key | P10.0KHCT-ND (https://octopart-clicks.com/click/altium?manufacturer=Panasonic%20Electronic%20Components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) | 8 | 8770313 | 0,72 | 0,09 | EUR
Resistors | Panasonic Electronic Components (https://octopart-clicks.com/click/altium?manufacturer=Panasonic%20Electronic%20Components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) | ERJ-3GEY0R00V (https://octopart-clicks.com/click/altium?manufacturer=Panasonic%20Electronic%20Components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) | 0603 (1608 Metric) | 0R JUMPER 1/10W | 4 | Digi-Key | P0.0GCT-ND (https://octopart-clicks.com/click/altium?manufacturer=Panasonic%20Electronic%20Components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) | 8 | 6694836 | 0,72 | 0,09 | EUR

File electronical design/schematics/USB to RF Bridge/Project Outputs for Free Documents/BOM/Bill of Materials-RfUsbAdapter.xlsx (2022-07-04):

Category | Manufacturer 1 | Manufacturer Part Number 1 | Package / Case | Description | Quantity | Supplier 1 | Supplier Part Number 1 | Supplier Order Qty 1 | Supplier Stock 1 | Supplier Subtotal 1 | Supplier Unit Price 1 | Supplier Currency 1
Connectors, Interconnects | Samtec Inc. | SMA-J-P-H-ST-EM1 |  | CONN SMA JACK 50 OHM EDGE MNT | 1 | Digi-Key | SAM8857-ND | 2 | 1473 | 8,1 | 4,05 | EUR
Integrated Circuits (ICs) | FTDI, Future Technology Devices International Ltd | FT232RQ-REEL | 32-VFQFN Exposed Pad | IC USB FS SERIAL UART 32-QFN | 1 | Digi-Key | 768-1008-6-ND | 2 | 69510 | 8,1 | 4,05 | EUR
Connectors, Interconnects | Molex, LLC | 480372000 |  | CONN PLUG USB 4POS R/A SMD | 1 | Digi-Key | WM7086CT-ND | 2 | 7499 | 2,68 | 1,34 | EUR
Filters | Murata Electronics North America | DLW21SN121HQ2L | Horizontal, 4 PC Pad | CHOKE COIL COMMON MODE 280MA SMD | 1 | Digi-Key | 490-5135-1-ND | 2 | 6866 | 1,38 | 0,69 | EUR
Integrated Circuits (ICs) | Texas Instruments | TLV70033DCKR | 5-TSSOP, SC-70-5, SOT-353 | IC REG LDO 3.3V 0.2A SC70-5 | 1 | Digi-Key | 296-32413-1-ND | 2 | 9633 | 0,96 | 0,48 | EUR
Optoelectronics | Lite-On Inc. | LTST-C193KGKT-5A | 0603 (1608 Metric) | LED GREEN CLEAR 0603 SMD | 2 | Digi-Key | 160-1828-6-ND | 4 | 137510 | 1,48 | 0,37 | EUR
Optoelectronics | Lite-On Inc. | LTST-C193KRKT-5A | 0603 (1608 Metric) | LED RED CLEAR 0603 SMD | 1 | Digi-Key | 160-1830-1-ND | 2 | 147435 | 0,74 | 0,37 | EUR
Capacitors | Murata Electronics North America | GRM188R61C105KA93D | 0603 (1608 Metric) | CAP CER 1UF 16V 10% X5R 0603 | 3 | Digi-Key | 490-1536-1-ND | 6 | 721477 | 0,84 | 0,14 | EUR
Resistors | Panasonic Electronic Components | ERJ-3EKF1002V | 0603 (1608 Metric) | 10K OHM 1% 1/10W 0603 | 5 | Digi-Key | P10.0KHCT-ND | 10 | 8770313 | 0,9 | 0,09 | EUR
Resistors | Panasonic Electronic Components | ERJ-3EKF3300V | 0603 (1608 Metric) | RES SMD 330 OHM 1% 1/10W 0603 | 2 | Digi-Key | P330HCT-ND | 4 | 101601 | 0,36 | 0,09 | EUR
Resistors | Panasonic Electronic Components | ERJ-3EKF4701V | 0603 (1608 Metric) | RES SMD 4.7K OHM 1% 1/10W 0603 | 1 | Digi-Key | P4.70KHCT-ND | 2 | 1871777 | 0,18 | 0,09 | EUR
Resistors | Panasonic Electronic Components | ERJ-3EKF6200V | 0603 (1608 Metric) | 620 OHM 1% 1/10W 0603 | 1 | Digi-Key | P620HCT-ND | 2 | 3677 | 0,18 | 0,09 | EUR
Kondensatoren | Murata Electronics North America | GRM1857U1A103JA44D |  | CAP CER 10NF 10V 5% U2J 0603 | 1 | Digi-Key | 490-8269-1-ND | 2 | 3533 | 0,4 | 0,2 | EUR
Kondensatoren | Kemet (https://octopart-clicks.com/click/altium?sku=2479898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) | C0603C104J4RACTU (https://octopart-clicks.com/click/altium?sku=2479898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) |  | 100nF 16V 5% X7R 0603 | 3 | Digi-Key | 399-1097-1-ND (https://octopart-clicks.com/click/altium?sku=2479898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) | 6 | 743090 | 0,6 | 0,1 | EUR
Capacitors | Murata Electronics North America | GRM188R60J475ME19D | 0603 | CAP CER 4.7UF 6.3V X5R 0603 | 1 | Digi-Key | 490-5421-2-ND | 2 | 4000 |  |  | EUR
Filters | Taiyo Yuden | FBMH1608HM102-T | 0603 (1608 Metric) | FERRITE BEAD 1 KOHM 0603 1LN | 1 | Digi-Key | 587-1739-2-ND | 2 | 132000 |  |  | EUR

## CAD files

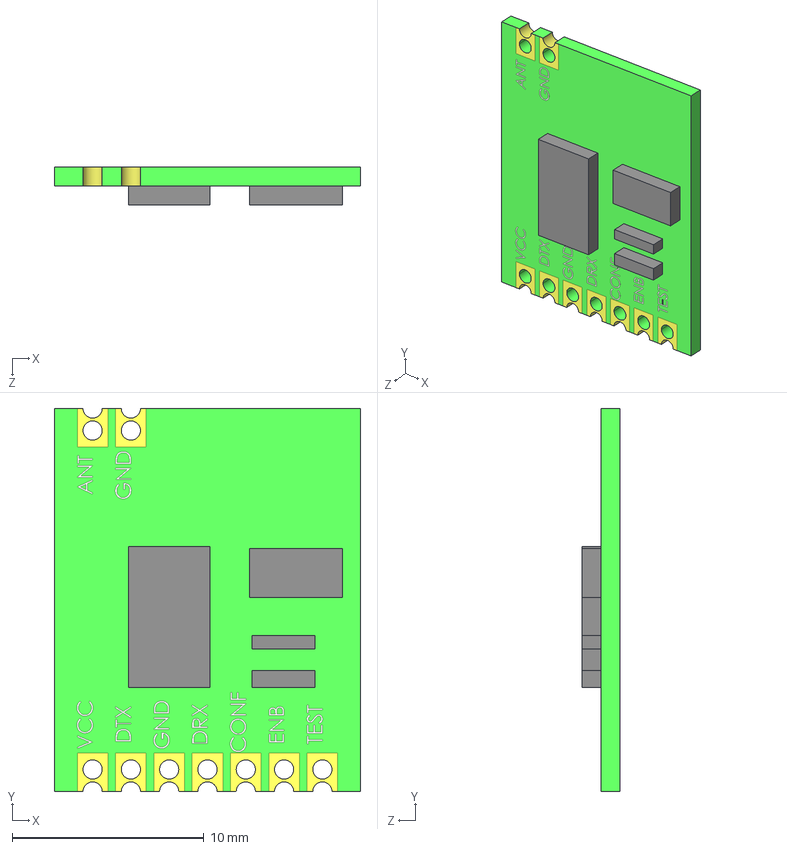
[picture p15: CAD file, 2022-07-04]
electronical design/components/09_RF/HM-TRP.STEP
16.0 x 20.0 x 2.00 mm

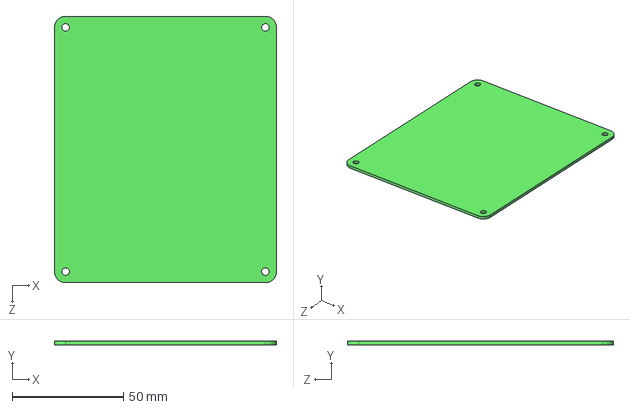
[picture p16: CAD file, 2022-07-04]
electronical design/schematics/main board/Models/TivaBaseBoard.STEP
100.0 x 1.60 x 120.0 mm

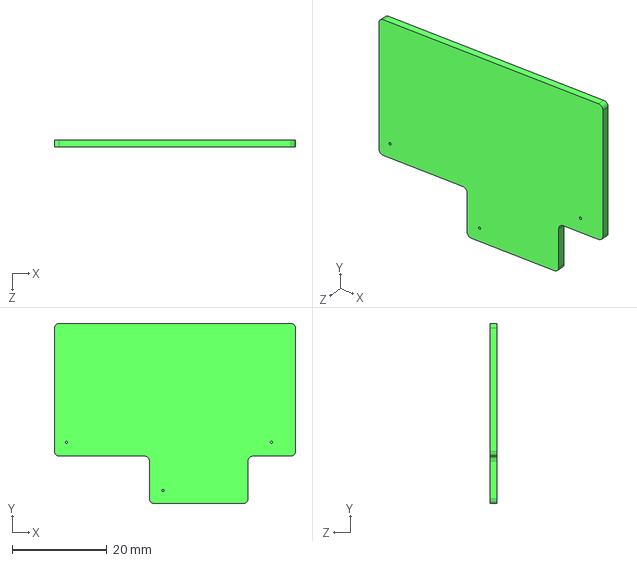
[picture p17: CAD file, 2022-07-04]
electronical design/schematics/UART to RF Bridge/Models/RfLaunchPadAdapter.STEP
50.8 x 38.0 x 1.55 mm

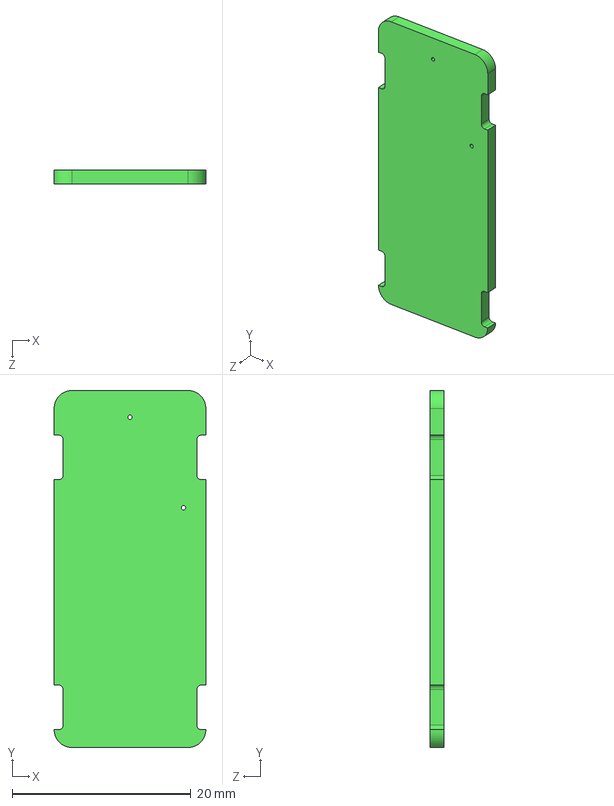
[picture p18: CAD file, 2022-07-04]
electronical design/schematics/USB to RF Bridge/Models/RfUsbStickPCB.STEP
17.0 x 40.0 x 1.55 mm

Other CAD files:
software/Debug_UART9600/main.obj
software/Debug_UART9600/Driver/fatfs/ff.obj
software/Debug_UART9600/Driver/KY040.obj
software/Debug_UART9600/Manager/DisplayManager.obj
software/Debug_UART9600/startup_ccs.obj
software/Debug_UART9600/utils/ustdlib.obj
software/Debug_UART9600/Driver/fatfs/cc932.obj
software/Debug_UART9600/Driver/NHD0216K3Z.obj
software/Debug_UART9600/Manager/TaskManager.obj
software/Debug_UART9600/utils/cmdline.obj
software/Debug_UART9600/Driver/ACT.obj
software/Debug_UART9600/Driver/fatfs/mmc-ek-tm4c123gxl.obj
software/Debug_UART9600/Manager/FileManager.obj
software/Debug_UART9600/System.obj
electronical design/components/09_RF/HM-TRP.SLDPRT
electronical design/components/10_Connector/480372000.stp
software/Debug_UART9600/Driver/DS3231.obj
software/Debug_UART9600/Driver/HCSR501.obj
software/Debug_UART9600/Driver/HMTRP.obj
software/Debug_UART9600/Driver/LED.obj
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

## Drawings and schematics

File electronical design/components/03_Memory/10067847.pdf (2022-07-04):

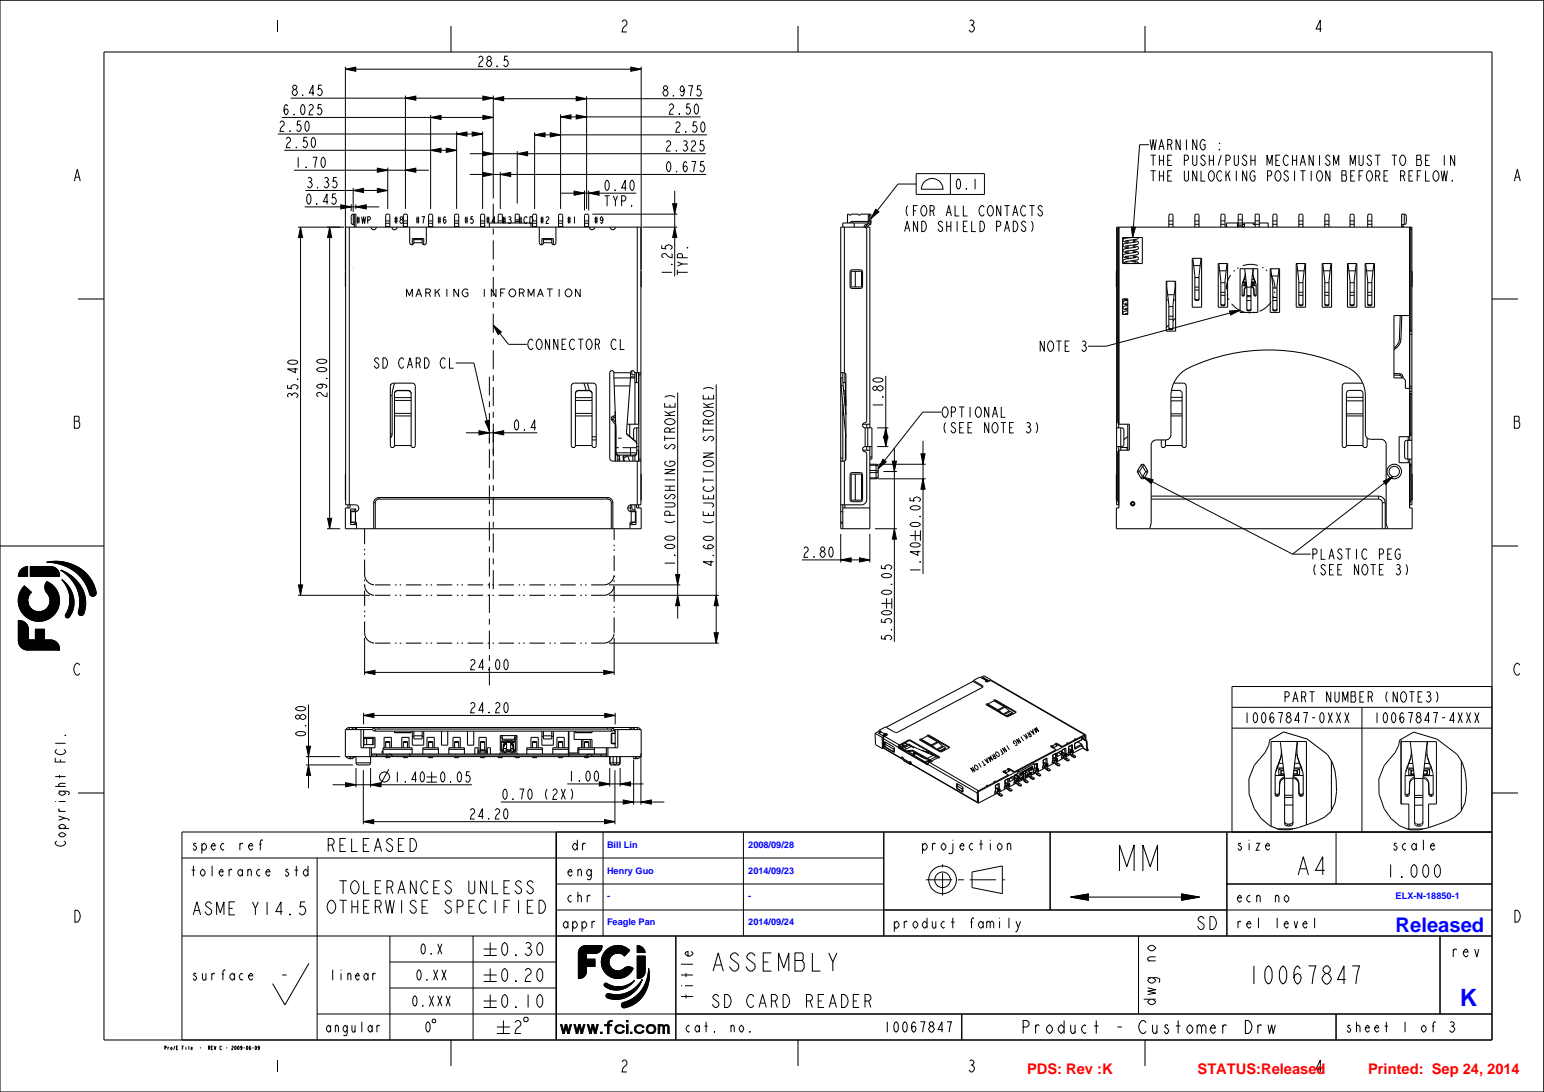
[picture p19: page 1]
Henry Guo; Bill Lin; PDS: Rev :K; STATUS:Released; Printed: Sep 24, 2014

- | | | ELX-N-18850-1

Feagle Pan | 2014/09/24

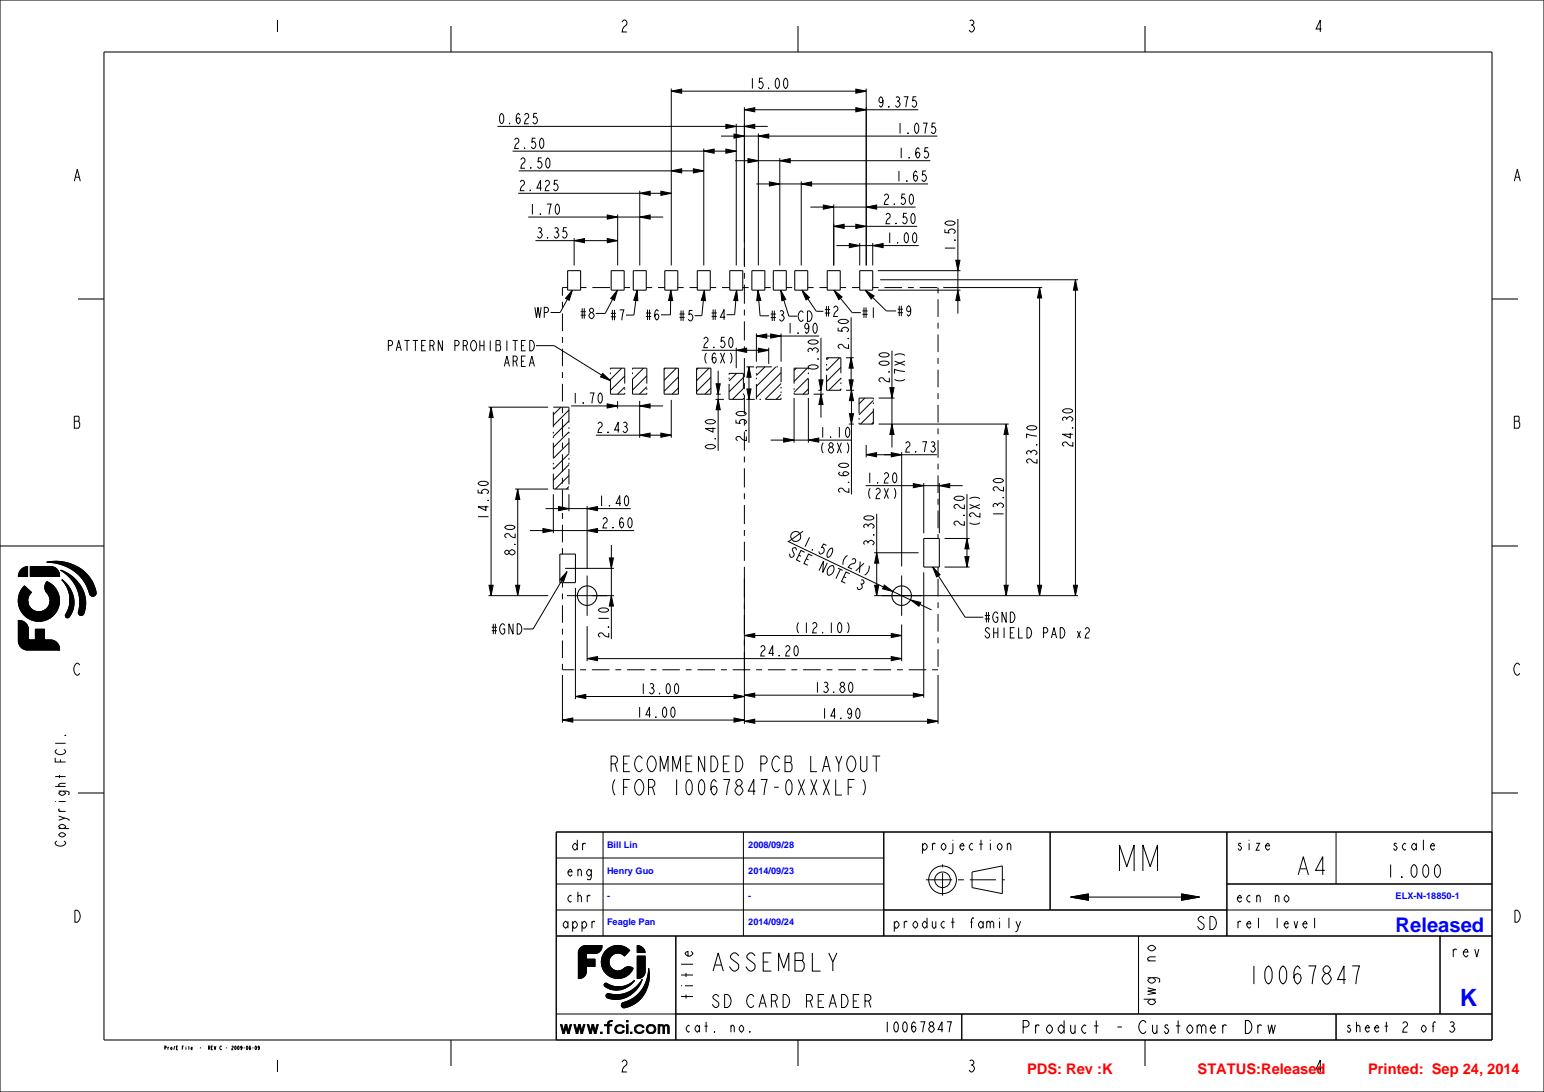
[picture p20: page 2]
Henry Guo; Feagle Pan; Bill Lin

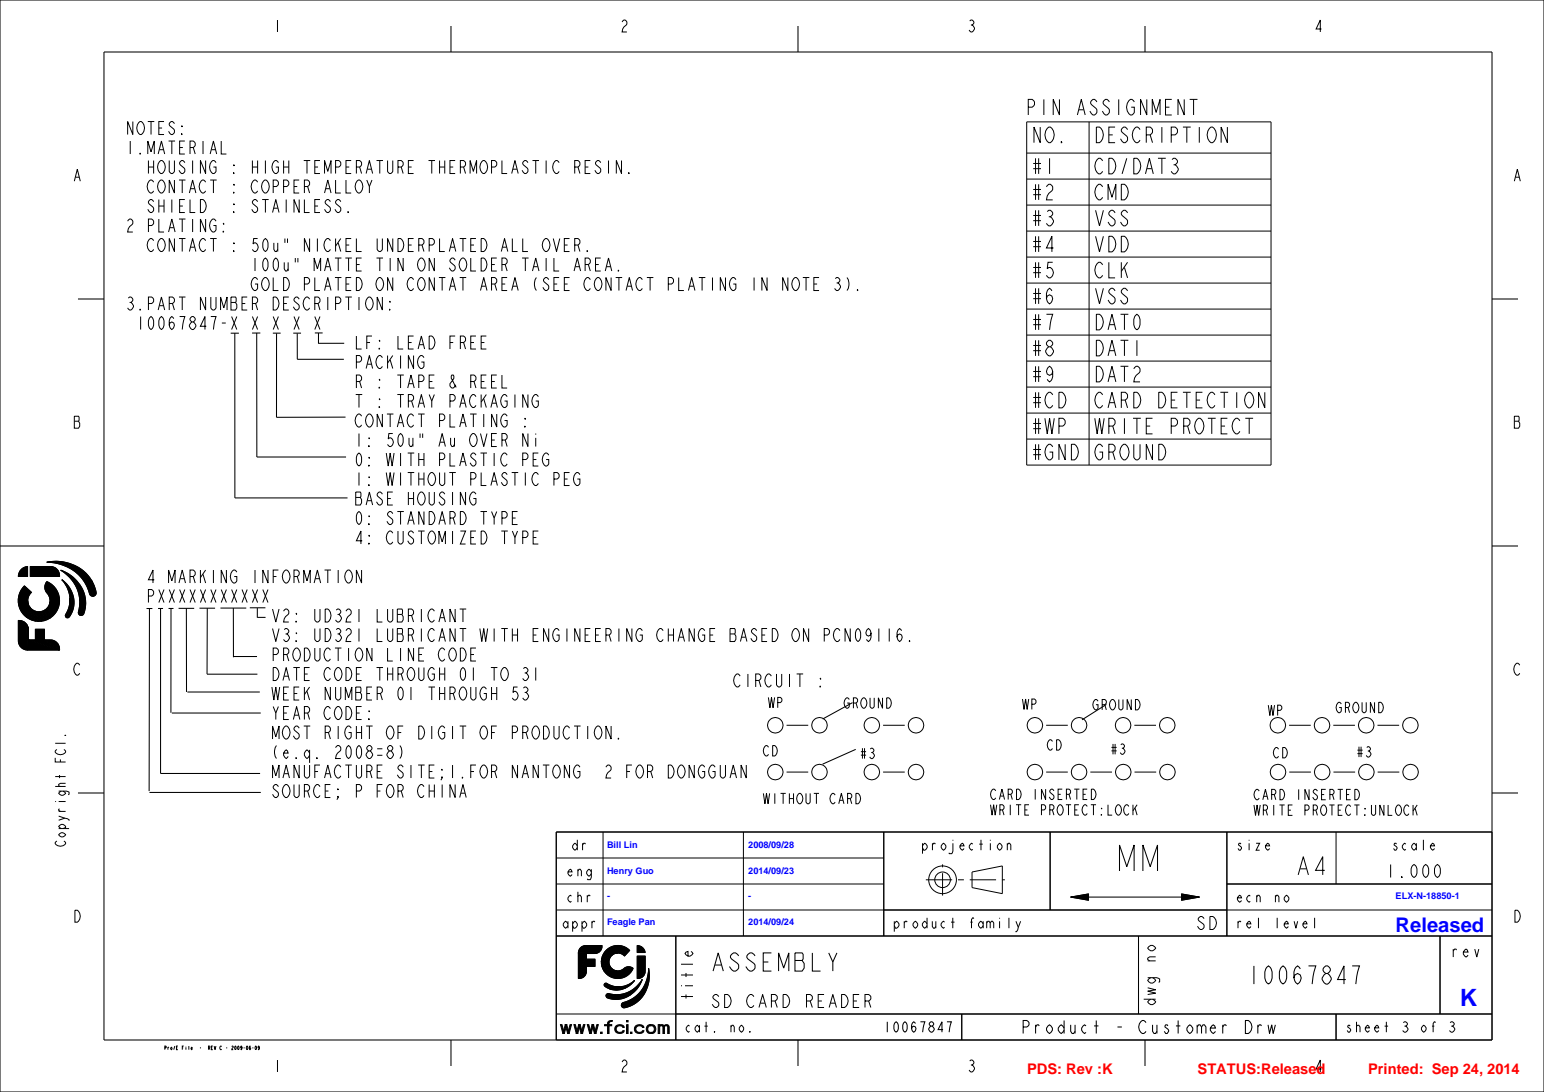
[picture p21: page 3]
Henry Guo; Feagle Pan; Bill Lin

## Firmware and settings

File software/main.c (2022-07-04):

//*****************************************************************************
//
// sd_card.c - Example program for reading files from an SD card.
//
// Copyright (c) 2011-2015 Texas Instruments Incorporated.  All rights reserved.
// Software License Agreement
// 
// Texas Instruments (TI) is supplying this software for use solely and
// exclusively on TI's microcontroller products. The software is owned by
// TI and/or its suppliers, and is protected under applicable copyright
// laws. You may not combine this software with "viral" open-source
// software in order to form a larger program.
// 
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
// 
// This is part of revision 2.1.1.71 of the DK-TM4C123G Firmware Package.
//
//*****************************************************************************

#include <stdint.h>
#include <stdbool.h>
#include <string.h>
#include "inc/hw_ints.h"
#include "inc/hw_memmap.h"
#include "driverlib/fpu.h"
#include "driverlib/gpio.h"
#include "driverlib/interrupt.h"
#include "driverlib/pin_map.h"
#include "driverlib/rom.h"
#include "driverlib/sysctl.h"
#include "driverlib/systick.h"
#include "driverlib/uart.h"
#include "utils/cmdline.h"
#include "utils/uartstdio.h"
#include "utils/ustdlib.h"
#include "Driver/ACT.h"
#include "Driver/fatfs/ff.h"
#include "Driver/fatfs/diskio.h"
#include "Driver/VS10xx.h"
#include "Driver/DS3231.h"
#include "Manager/ConsoleManager.h"
#include "Manager/FileManager.h"
#include "Manager/AudioManager.h"
#include "Manager/DisplayManager.h"
#include "Manager/TaskManager.h"
#include "Driver/LED.h"
#include "Driver/NHD0216K3Z.h"
#include "Driver/HCSR501.h"
#include "Driver/KY040.h"
#include "Driver/Timer.h"
#include "Msg.h"
#include "System.h"


//*****************************************************************************
//
// printf functions used in this file
//
//*****************************************************************************
#define eprintf(fms, ...)	do{	UARTprintf("\033[31;1m"); \
								UARTprintf("[ MAIN ] ERROR " fms, __VA_ARGS__); \
								UARTprintf("\033[0m");} while(0)

#define dprintf(fms, ...)	UARTprintf("[ MAIN ] " fms, __VA_ARGS__); \

//
// The error routine that is called if the driver library encounters an error.
//
//*****************************************************************************
#ifdef DEBUG
void

__error__(char *pcFilename, uint32_t ui32Line)
{
}
#endif

#define FW_VERSION				("0.1")

//*****************************************************************************
//
// Defines the size of the buffer that holds the command line.
//
//*****************************************************************************
#define CMD_BUF_SIZE            (64)


//*****************************************************************************
//
// The buffer that holds the command line.
//
//*****************************************************************************
static char g_pcCmdBuf[CMD_BUF_SIZE];

//*****************************************************************************
//
// Configure the UART and its pins.  This must be called before UARTprintf().
//
//*****************************************************************************
void
ConfigureUART(void)
{
    //
    // Enable the GPIO Peripheral used by the UART.
    //
    ROM_SysCtlPeripheralEnable(SYSCTL_PERIPH_GPIOA);

    //
    // Enable UART0
    //
    ROM_SysCtlPeripheralEnable(SYSCTL_PERIPH_UART0);

    //
    // Configure GPIO Pins for UART mode.
    //
    ROM_GPIOPinConfigure(GPIO_PA0_U0RX);
    ROM_GPIOPinConfigure(GPIO_PA1_U0TX);
    ROM_GPIOPinTypeUART(GPIO_PORTA_BASE, GPIO_PIN_0 | GPIO_PIN_1);

    //
    // Use the internal 16MHz oscillator as the UART clock source.
    //
    UARTClockSourceSet(UART0_BASE, UART_CLOCK_PIOSC);

    //
    // Initialize the UART for console I/O.
    //

//#ifdef UART_9600
//    UARTStdioConfig(0, 9600, 16000000);
//#else
    UARTStdioConfig(0, 115200, 16000000);
//#endif
}


//*****************************************************************************
//
// Get time and date from DS3231 RTC.
//
// \param ucRegister is the offset to the register to write.
// \param pucData is a pointer to the returned data.
//
//  \return \b true on success or \b false on error.
//
//****************************************************************************

void
PortDIntHandler(void)
{
	uint32_t ui32IntStatus;

	//
	// Get current interrupt state
	//
	ui32IntStatus = GPIOIntStatus(GPIO_PORTD_BASE, false);

	//
	// Clear the flag that triggered the interrupt
	//
	GPIOIntClear(GPIO_PORTD_BASE, ui32IntStatus);

	//
	// Call coresponding callback-function
	//
	if(ui32IntStatus & GPIO_INT_PIN_1)
	{
		HCSR501OnMotion();
	}

	if(ui32IntStatus & GPIO_INT_PIN_2)
	{
		FM_SDCheck();
	}
}

//*****************************************************************************
//
// Get time and date from DS3231 RTC.
//
// \param ucRegister is the offset to the register to write.
// \param pucData is a pointer to the returned data.
//
//  \return \b true on success or \b false on error.
//
//****************************************************************************
void
ConvertSecondsInHhMmSs(uint32_t ui32TotalSeconds, int8_t* pi8Hour, int8_t* pi8Minutes, int8_t* pi8Seconds)
{
	*pi8Seconds = (ui32TotalSeconds % 60);
	*pi8Minutes = (ui32TotalSeconds % 3600) / 60;
	*pi8Hour = (ui32TotalSeconds % 86400) / 3600;
}


//*****************************************************************************
//
// The program main function.  It performs initialization, then runs a command
// processing loop to read commands from the console.
//
//*****************************************************************************

int
main(void)
{
    int nStatus;
    int8_t i8TaskIdx;
	uint8_t ui8Cnt, bTaskRunning, bSubseqTaskFound;
    TIME sMotionExitTime;
    TIME sEventTimeout;
    uint32_t ui32CurrentTimeInSeconds;
    uint16_t ui16IndexedFiles = 0;

    //
    // Enable lazy stacking for interrupt handlers.  This allows floating-point
    // instructions to be used within interrupt handlers, but at the expense of
    // extra stack usage.
    //
    FPULazyStackingEnable();

    //
    // Set the system clock to run at 80MHz from the PLL.
    //
    SysCtlClockSet(	SYSCTL_SYSDIV_2_5 |
    				SYSCTL_USE_PLL |
					SYSCTL_OSC_MAIN |
					SYSCTL_XTAL_16MHZ );

    //
    // Enable Interrupts
    //
    IntMasterEnable();
    IntEnable(INT_GPIOD);

    //
    // Initialize the UART as a console for text I/O.
    //
    ConfigureUART();


    dprintf("Systeminitialisierung ...\n", 0);

    //
	// Initialize DS3231 RTC
	//
    LEDInit();

    //
    // Initialize file manager
    //
    FM_Init();

    //
    // Initialize the VS1003 audio codec
    //
    VS10xxInit();

	//
	// Init task manager
	//
	TM_Init();

    //
    // Init timers
    //
    TimerInit();

    //
	// Initialize RLY8 relais board
	//
    ActInit();

    //
	// Initialize DS3231 RTC
	//
    DS3231Init();

    //
	// Initialize HCSR501 motion sensor
	//
    HCSR501Init();

    //
    // Init rotary encoder
    //
    //KY040Init();

	//
	// Initialize sMotionExitTime structure to -1
	//
	memset(&sMotionExitTime, -1, sizeof(sMotionExitTime));

	//
	// Mount file system, load configuration files and index available
	// files in root "/" directory
	//
    if(FM_SDCheck() == FR_OK)
    {
    	//
    	// Load configuration files
    	//
    	FM_ConfigLoad();

    	//
    	// Index files
    	//
    	ui16IndexedFiles = FM_Index();
    }

    //
    // Init Audio Manager
    //
    AM_Init(g_sSystem.ui8DefaultVolume, g_sSystem.ui8DefaultFadeTime, ui16IndexedFiles);

    //
	// Initialize display manager
	//
    DM_Init(g_sSystem.ui8DefaultDsplContrast, g_sSystem.ui8DefaultDsplBrightness);


    //
    // Clear display
    //
    NHD0216K3ZSendCommand(NHD0216K3Z_CLEAR_SCREEN, -1);

    //
    // Print hello message to user.
    //
    UARTprintf("\n\n########  ##    ##  ######   #######\n");
    UARTprintf("##     ##  ##  ##  ##    ## ##     ##\n");
    UARTprintf("##     ##   ####   ##       ##     ##\n");
    UARTprintf("########     ##    ##       ##     ##\n");
    UARTprintf("##           ##    ##       ##     ##\n");
    UARTprintf("##           ##    ##    ## ##     ##\n");
    UARTprintf("##           ##     ######   #######\n\n");

    UARTprintf("              Pyramidensteuerung v%s\n\n", FW_VERSION);

    UARTprintf("\nSchreibe \'?\' fuer Hilfe.\n\n");


    //
    // Reset task-running flag on startup
    //
    bTaskRunning = false;
    dprintf("Suche nach Aufgaben ... \n", 0);


	//
	// Print a prompt to the console.  Show the CWD.
	//
    // UARTprintf("\n%s> ", g_pcCwdBuf);

	//*********************************************************************************
    //
	// Enter an infinite loop.
	//
    //*********************************************************************************
	while(1)
	{
		//
		// Update display
		//
		DM_UpdateDisplay();

		//
		// Check for  mode
		// 0: Manuel
		// 1: Auto
		//
		if(g_sSystem.ui8Mode)
		{
			//
			// Simple do-while(0) approach to be able to exit and
			// return to beginning at any location
			//
			do {
				//
				// Check if a task is running
				//
				if(false == bTaskRunning)
				{
					//
					// Search task list for matching entries
					//
					i8TaskIdx = TM_TaskSearch(g_sDS3231Data.i32TimeInSeconds);

					//
					// In case a task was found got to "RUN" mode and use i8TaskIdx for further processing
					//
					if(i8TaskIdx >= 0)
					{
						dprintf("Aufgabe %i aktiviert, %02i:%02i - %02i:%02i\n", i8TaskIdx + 1, g_sTask[i8TaskIdx].sStartTime.i8Hour, g_sTask[i8TaskIdx].sStartTime.i8Minute, g_sTask[i8TaskIdx].sStopTime.i8Hour, g_sTask[i8TaskIdx].sStopTime.i8Minute);

						//
						// Go to "RUN" mode
						//
						bTaskRunning = true;

						//
						// Go to beginning
						//
						break;
					}
				}

				//
				// If task with index i8TaskIdx is running
				//
				else
				{
					//
					// Check if task stop time is reached
					//
					ui32CurrentTimeInSeconds = g_sDS3231Data.i32TimeInSeconds;

					if(ui32CurrentTimeInSeconds >= g_sTask[i8TaskIdx].sStopTime.i32TimeInSeconds)
					{
						dprintf("Aufgabe %i beendet.\n", i8TaskIdx + 1);

						//
						// Search in task list for matching entries
						//
						bSubseqTaskFound = false;

						dprintf("Suchen nach Aufgaben, die direkt nach Aufgabe %i folgen.\n", i8TaskIdx + 1);

						for(i8TaskIdx = 0; i8TaskIdx < N_TASK; i8TaskIdx++)
						{
							if(g_sTask[i8TaskIdx].sStartTime.i32TimeInSeconds >= 0)
							{
								if(g_sTask[i8TaskIdx].sStartTime.i32TimeInSeconds == ui32CurrentTimeInSeconds)
								{
									dprintf("Aufgabe %i gefunden.\n", i8TaskIdx + 1);
									bSubseqTaskFound = true;
									break;
								}
							}
						}

						//
						// Check subsequent task flag
						//
						if(false == bSubseqTaskFound)
						{

							dprintf("Keine direkt folgenden Aufgaben gefunden.\n", 0);

							//
							// Reset motion flags
							//
							g_bActiveMotionEvent = false;
							g_bExitMotionEvent = false;

							//
							// Disable motion sensor in case it is active
							//
							if(false != g_bHCSR501Enable)
							{
								//
								// Disable motion sensor
								//
								HCSR501Disable();
							}

							//
							// Disbale all actuator(s)
							//
							ActDisableAll();

							//
							// Fadeout and stop audio playback
							//
							AM_VolumeFade(g_sSystem.ui8DefaultFadeTime, AM_FADEOUT);

							//
							// Go to "SEARCH" mode
							//
							bTaskRunning = false;
							dprintf("Suche nach Aufgaben ... \n", 0);

							//
							// Go to beginning
							//
							break;
						}

						//
						// Go to beginning
						//
						break;
					} // if(ui32CurrentTimeInSeconds >= g_sTask[i8TaskIdx].sStopTime.i32TimeInSeconds)

					//
					// If task stop time is not reached
					//
					else
					{
						//
						// If motion sensing is enabled
						//
						if(false != g_sTask[i8TaskIdx].bMotion)
						{
							//
							// Check motion sensor state
							//
							if (false == g_bHCSR501Enable)
							{
								//
								// Enable motion sensor
								//
								HCSR501Enable();
							}

							//
							// MOTION ACTIVE EVENT
							//
							if(false != g_bActiveMotionEvent)
							{
								//
								// Rest motion exit time
								//
								memset(&sMotionExitTime, -1, sizeof(sMotionExitTime));
							}

							//
							// MOTION EXIT EVENT
							//
							else if(g_bExitMotionEvent) // if(g_bActiveMotionEvent)
							{
								//
								// Set motion exit time
								//
								if(sMotionExitTime.i8Hour == -1 && sMotionExitTime.i8Minute == -1 && sMotionExitTime.i8Second == -1)
								{
									//
									// Get current time
									//
									sMotionExitTime.i32TimeInSeconds = g_sDS3231Data.i32TimeInSeconds;
									ConvertSecondsInHhMmSs(sMotionExitTime.i32TimeInSeconds, &sMotionExitTime.i8Hour, &sMotionExitTime.i8Minute, &sMotionExitTime.i8Second);

									//
									// Calculate timeout time
									//
									sEventTimeout.i32TimeInSeconds = sMotionExitTime.i32TimeInSeconds + g_sTask[i8TaskIdx].sActiveTime.i32TimeInSeconds;
									ConvertSecondsInHhMmSs(sEventTimeout.i32TimeInSeconds, &sEventTimeout.i8Hour, &sEventTimeout.i8Minute, &sEventTimeout.i8Second);

									dprintf("Gueltiges Bewegungsereignis beende um %02i:%02i:%02i\n",sMotionExitTime.i8Hour, sMotionExitTime.i8Minute, sMotionExitTime.i8Second);
									dprintf("Event endet um %02i:%02i:%02i\n", sEventTimeout.i8Hour, sEventTimeout.i8Minute, sEventTimeout.i8Second);
								}

								//
								// Check if motion event time reached
								//
								if(sEventTimeout.i32TimeInSeconds <= g_sDS3231Data.i32TimeInSeconds)
								{
									//
									//Stop Event and reset all motion flags
									//
									g_bActiveMotionEvent = false;
									g_bExitMotionEvent = false;

									//
									// Disable all actuator(s)
									//
									ActDisableAll();

									//
									// Fadeout and Stop playback
									//
									AM_VolumeFade(g_sSystem.ui8DefaultFadeTime, AM_FADEOUT);

									dprintf("Bewegungsereignis beendet.\n", 0);

									//
									// Go to beginning
									//
									break;
								}
							} // if(false != g_bActiveMotionEvent)
							else
							{
								//
								// Go to beginning
								//
								break;
							}
						} // if(g_sTask[ui8Idx].bMotion)
						else
						{
							//
							// Check motion sensor state
							//
							if(g_bHCSR501Enable)
							{
								//
								// Disable motion sensor
								//
								HCSR501Disable();
							}
						}

						//
						// If Audio playback is enabled
						//
						if(false != g_sTask[i8TaskIdx].bAudio)
						{
							//
							// Start audio playback
							//
							AM_Play();
						}
						else
						{
							//
							// Fade out and stop audio playback
							//
							AM_VolumeFade(g_sSystem.ui8DefaultFadeTime, AM_FADEOUT);
						}


						//
						// If actor usage is enabled
						//
						if(false != g_sTask[i8TaskIdx].bActuator)
						{
							//
							// Enable Actuator(s)
							//
							for(ui8Cnt = 0; ui8Cnt < ACT_N_CH; ui8Cnt++)
							{
								if(g_sTask[i8TaskIdx].bActuatorCH[ui8Cnt] == true)
								{
									ActEnbale(ui8Cnt + 1);
								}
								else
								{
									ActDisable(ui8Cnt + 1);
								}
							}
						}
						else
						{
							//
							// Disable all actor
							//
							// ActDisableAll();
						}
					} // if(ui32CurrentTimeInSeconds >= g_sTask[i8TaskIdx].sStopTime.i32TimeInSeconds)
				} // if(false == bTaskRunning)
			}
			while(0);
		}


		//**********************************************************************
		//
		// Commandline processing
		//
		//**********************************************************************

        //
        // Peek to see if a full command is ready for processing
        //
		if(UARTPeek('\r') != -1)
		{
			//
			// Get a line of text from the user.
			//
			UARTgets(g_pcCmdBuf, sizeof(g_pcCmdBuf));

			//
			// Pass the line from the user to the command processor.  It will be
			// parsed and valid commands executed.
			//
			nStatus = CmdLineProcess(g_pcCmdBuf);

			//
			// Handle the case of bad command.
			//

			if(nStatus == CMDLINE_BAD_CMD)
			{
				dprintf("Falsches Kommando!\n", 0);
			}

			//
			// Handle the case of too many arguments.
			//
			else if(nStatus == CMDLINE_TOO_MANY_ARGS)
			{
				eprintf("Too many arguments for command processor!\n", 0);
			}

			//
			// Otherwise the command was executed.  Print the error code if one was
			// returned.
			//
			else if(nStatus != 0)
			{
				// UARTprintf("Command returned error code %s\n",
				//		StringFromFResult((FRESULT)nStatus));
			}

			//
			// Print a prompt to the console.  Show the CWD.
			//
			UARTprintf("\n%s> ", g_pcCwdBuf);
		}
	}
}

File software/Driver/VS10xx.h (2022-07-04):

#ifndef VS10XX_MICROCONTROLLER_DEFINITIONS_H
#define VS10XX_MICROCONTROLLER_DEFINITIONS_H

/*
  VLSI Solution microcontroller definitions for:
  VS1063, VS1053 (and VS8053), VS1033, VS1003, VS1103, VS1011.

  v1.01 2012-11-26 HH  Added VS1053 recording registers, bug fixes
  v1.00 2012-11-23 HH  Initial version
*/

#include <stdint.h>
#include <stdio.h>

#define VS10XX_MUTE_VAL	0xFEFE

#define WRITE_CODE      0x02
#define READ_CODE       0x03


/* SCI registers */

#define SCI_MODE        0x00
#define SCI_STATUS      0x01
#define SCI_BASS        0x02
#define SCI_CLOCKF      0x03
#define SCI_DECODE_TIME 0x04
#define SCI_AUDATA      0x05
#define SCI_WRAM        0x06
#define SCI_WRAMADDR    0x07
#define SCI_HDAT0       0x08 /* VS1063, VS1053, VS1033, VS1003, VS1011 */
#define SCI_IN0         0x08 /* VS1103 */
#define SCI_HDAT1       0x09 /* VS1063, VS1053, VS1033, VS1003, VS1011 */
#define SCI_IN1         0x09 /* VS1103 */
#define SCI_AIADDR      0x0A
#define SCI_VOL         0x0B
#define SCI_AICTRL0     0x0C /* VS1063, VS1053, VS1033, VS1003, VS1011 */
#define SCI_MIXERVOL    0x0C /* VS1103 */
#define SCI_AICTRL1     0x0D /* VS1063, VS1053, VS1033, VS1003, VS1011 */
#define SCI_ADPCMRECCTL 0x0D /* VS1103 */
#define SCI_AICTRL2     0x0E
#define SCI_AICTRL3     0x0F


/* SCI register recording aliases */

#define SCI_RECQUALITY 0x07 /* (WRAMADDR) VS1063 */
#define SCI_RECDATA    0x08 /* (HDAT0)    VS1063 */
#define SCI_RECWORDS   0x09 /* (HDAT1)    VS1063 */
#define SCI_RECRATE    0x0C /* (AICTRL0)  VS1063, VS1053 */
#define SCI_RECDIV     0x0C /* (AICTRL0)  VS1033, VS1003 */
#define SCI_RECGAIN    0x0D /* (AICTRL1)  VS1063, VS1053, VS1033, VS1003 */
#define SCI_RECMAXAUTO 0x0E /* (AICTRL2)  VS1063, VS1053, VS1033 */
#define SCI_RECMODE    0x0F /* (AICTRL3)  VS1063, VS1053 */


/* SCI_MODE bits */

#define SM_DIFF_B             0
#define SM_LAYER12_B          1 /* VS1063, VS1053, VS1033, VS1011 */
#define SM_RECORD_PATH_B      1 /* VS1103 */
#define SM_RESET_B            2
#define SM_CANCEL_B           3 /* VS1063, VS1053 */
#define SM_OUTOFWAV_B         3 /* VS1033, VS1003, VS1011 */
#define SM_OUTOFMIDI_B        3 /* VS1103 */
#define SM_EARSPEAKER_LO_B    4 /* VS1053, VS1033 */
#define SM_PDOWN_B            4 /* VS1003, VS1103 */
#define SM_TESTS_B            5
#define SM_STREAM_B           6 /* VS1053, VS1033, VS1003, VS1011 */
#define SM_ICONF_B            6 /* VS1103 */
#define SM_EARSPEAKER_HI_B    7 /* VS1053, VS1033 */
#define SM_DACT_B             8
#define SM_SDIORD_B           9
#define SM_SDISHARE_B        10
#define SM_SDINEW_B          11
#define SM_ENCODE_B          12 /* VS1063 */
#define SM_ADPCM_B           12 /* VS1053, VS1033, VS1003 */
#define SM_EARSPEAKER_1103_B 12 /* VS1103 */
#define SM_ADPCM_HP_B        13 /* VS1033, VS1003 */
#define SM_LINE1_B           14 /* VS1063, VS1053 */
#define SM_LINE_IN_B         14 /* VS1033, VS1003, VS1103 */
#define SM_CLK_RANGE_B       15 /* VS1063, VS1053, VS1033 */
#define SM_ADPCM_1103_B      15 /* VS1103 */

#define SM_DIFF           (1<< 0)
#define SM_LAYER12        (1<< 1) /* VS1063, VS1053, VS1033, VS1011 */
#define SM_RECORD_PATH    (1<< 1) /* VS1103 */
#define SM_RESET          (1<< 2)
#define SM_CANCEL         (1<< 3) /* VS1063, VS1053 */
#define SM_OUTOFWAV       (1<< 3) /* VS1033, VS1003, VS1011 */
#define SM_OUTOFMIDI      (1<< 3) /* VS1103 */
#define SM_EARSPEAKER_LO  (1<< 4) /* VS1053, VS1033 */
#define SM_PDOWN          (1<< 4) /* VS1003, VS1103 */
#define SM_TESTS          (1<< 5)
#define SM_STREAM         (1<< 6) /* VS1053, VS1033, VS1003, VS1011 */
#define SM_ICONF          (1<< 6) /* VS1103 */
#define SM_EARSPEAKER_HI  (1<< 7) /* VS1053, VS1033 */
#define SM_DACT           (1<< 8)
#define SM_SDIORD         (1<< 9)
#define SM_SDISHARE       (1<<10)
#define SM_SDINEW         (1<<11)
#define SM_ENCODE         (1<<12) /* VS1063 */
#define SM_ADPCM          (1<<12) /* VS1053, VS1033, VS1003 */
#define SM_EARSPEAKER1103 (1<<12) /* VS1103 */
#define SM_ADPCM_HP       (1<<13) /* VS1033, VS1003 */
#define SM_LINE1          (1<<14) /* VS1063, VS1053 */
#define SM_LINE_IN        (1<<14) /* VS1033, VS1003, VS1103 */
#define SM_CLK_RANGE      (1<<15) /* VS1063, VS1053, VS1033 */
#define SM_ADPCM_1103     (1<<15) /* VS1103 */

#define SM_ICONF_BITS 2
#define SM_ICONF_MASK 0x00c0

#define SM_EARSPEAKER_1103_BITS 2
#define SM_EARSPEAKER_1103_MASK 0x3000


/* SCI_STATUS bits */

#define SS_REFERENCE_SEL_B  0 /* VS1063, VS1053 */
#define SS_AVOL_B           0 /* VS1033, VS1003, VS1103, VS1011 */
#define SS_AD_CLOCK_B       1 /* VS1063, VS1053 */
#define SS_APDOWN1_B        2
#define SS_APDOWN2_B        3
#define SS_VER_B            4
#define SS_VCM_DISABLE_B   10 /* VS1063, VS1053 */
#define SS_VCM_OVERLOAD_B  11 /* VS1063, VS1053 */
#define SS_SWING_B         12 /* VS1063, VS1053 */
#define SS_DO_NOT_JUMP_B   15 /* VS1063, VS1053 */

#define SS_REFERENCE_SEL (1<< 0) /* VS1063, VS1053 */
#define SS_AVOL          (1<< 0) /* VS1033, VS1003, VS1103, VS1011 */
#define SS_AD_CLOCK      (1<< 1) /* VS1063, VS1053 */
#define SS_APDOWN1       (1<< 2)
#define SS_APDOWN2       (1<< 3)
#define SS_VER           (1<< 4)
#define SS_VCM_DISABLE   (1<<10) /* VS1063, VS1053 */
#define SS_VCM_OVERLOAD  (1<<11) /* VS1063, VS1053 */
#define SS_SWING         (1<<12) /* VS1063, VS1053 */
#define SS_DO_NOT_JUMP   (1<<15) /* VS1063, VS1053 */

#define SS_SWING_BITS     3
#define SS_SWING_MASK     0x7000
#define SS_VER_BITS       4
#define SS_VER_MASK       0x00f0
#define SS_AVOL_BITS      2
#define SS_AVOL_MASK      0x0003

#define SS_VER_VS1001 0x00
#define SS_VER_VS1011 0x10
#define SS_VER_VS1002 0x20
#define SS_VER_VS1003 0x30
#define SS_VER_VS1053 0x40
#define SS_VER_VS8053 0x40
#define SS_VER_VS1033 0x50
#define SS_VER_VS1063 0x60
#define SS_VER_VS1103 0x70


/* SCI_BASS bits */

#define ST_AMPLITUDE_B 12
#define ST_FREQLIMIT_B  8
#define SB_AMPLITUDE_B  4
#define SB_FREQLIMIT_B  0

#define ST_AMPLITUDE (1<<12)
#define ST_FREQLIMIT (1<< 8)
#define SB_AMPLITUDE (1<< 4)
#define SB_FREQLIMIT (1<< 0)

#define ST_AMPLITUDE_BITS 4
#define ST_AMPLITUDE_MASK 0xf000
#define ST_FREQLIMIT_BITS 4
#define ST_FREQLIMIT_MASK 0x0f00
#define SB_AMPLITUDE_BITS 4
#define SB_AMPLITUDE_MASK 0x00f0
#define SB_FREQLIMIT_BITS 4
#define SB_FREQLIMIT_MASK 0x000f


/* SCI_CLOCKF bits */

#define SC_MULT_B 13 /* VS1063, VS1053, VS1033, VS1103, VS1003 */
#define SC_ADD_B  11 /* VS1063, VS1053, VS1033, VS1003 */
#define SC_FREQ_B  0 /* VS1063, VS1053, VS1033, VS1103, VS1003 */

#define SC_MULT (1<<13) /* VS1063, VS1053, VS1033, VS1103, VS1003 */
#define SC_ADD  (1<<11) /* VS1063, VS1053, VS1033, VS1003 */
#define SC_FREQ (1<< 0) /* VS1063, VS1053, VS1033, VS1103, VS1003 */

#define SC_MULT_BITS 3
#define SC_MULT_MASK 0xe000
#define SC_ADD_BITS 2
#define SC_ADD_MASK  0x1800
#define SC_FREQ_BITS 11
#define SC_FREQ_MASK 0x07ff
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

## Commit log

2022-07-04 Added electronical design
    [480372000.stp, BOM_Complete-PYRAMIDE CONTROLLER.xlsx, BOM_Distributor_Import-PYRAMIDE CONTROLLER.xls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]
2022-07-04 Added source code directory
    [ACT.obj, AudioManager.obj, ConsoleManager.obj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]
2022-08-03 Added overall block diagram and main control loop flow diagram
2022-08-07 Added test flow chart
